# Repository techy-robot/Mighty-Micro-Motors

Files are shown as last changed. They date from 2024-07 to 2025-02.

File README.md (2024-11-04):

# Mighty Micro Motors
My goal with this project is to recreate the expensive and highly advanced motors typically found in big robots, such as in Boston Dynamics or MIT's robots, but at a **much** smaller scale. These are essentially tiny drone motors with a high reduction gearbox, a magnetic encoder, and a FOC controller board.

You can check out my project log [here](Progress%20Log.md).

This project is sponsored by [PCBWay](https://www.pcbway.com/)

## Gearbox
This has to be a resin printed or precision machined gearbox, just from the sheer smallness of everything. The brushless drone motors (HappyModel SE0802) are 10mm in diameter, so the gearbox ideally should be a similar size.

I'm currently thinking about having a cycloidal or split-ring planetary gearbox, due to the compact size and high reduction ratios

Preliminary CAD designs are on onshape, you can watch my progress here: [Mighty Micro Motors - Onshape](https://cad.onshape.com/documents/c861ec30af8169cf9c14bd7f/w/e538486c85e6a5fe77cd1d33/e/19bd07544dbaacbeb2fafd06). Step files and STL files will also be uploaded to this repo.

### Cycloidal 16-to-1 reduction:

Currently the design is twice as big as my ideal, with a 19mm diameter. I can not reduce the diameter without removing the bearings, possible reducing the lifespan. This *really* needs to be smaller, so I may do some testing and just remove some bearings. I'm not actually sure how well the 1x3x1mm bearings roll compared to just a smooth shaft. I could also cut the hole count down if the screws were also the shafts.

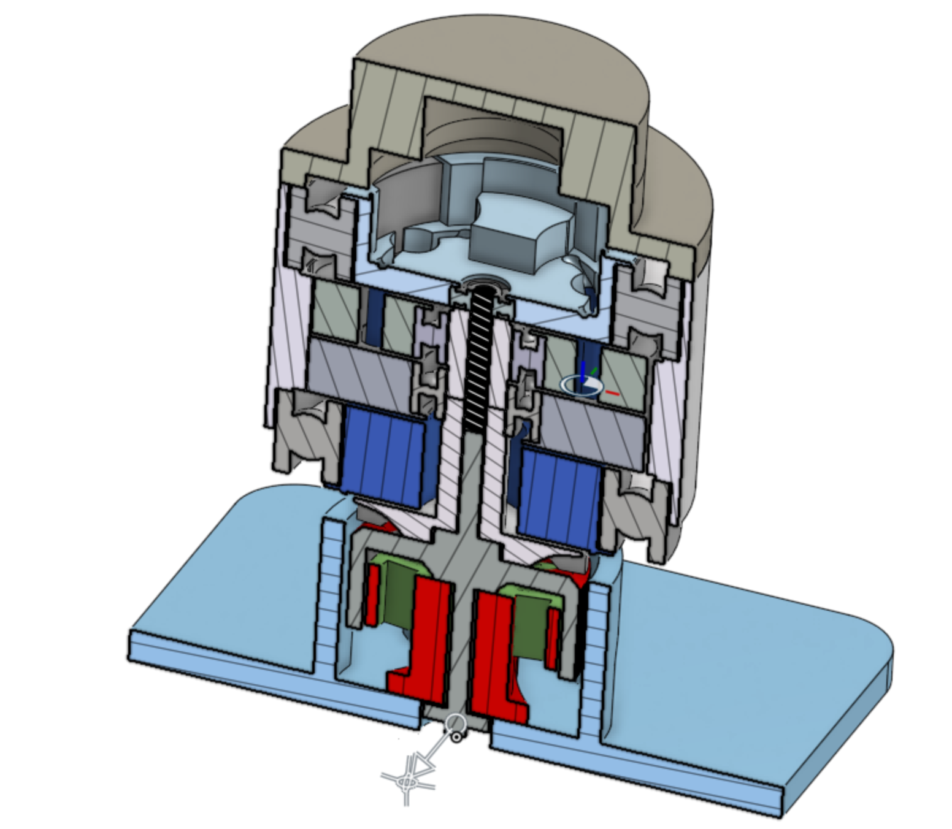
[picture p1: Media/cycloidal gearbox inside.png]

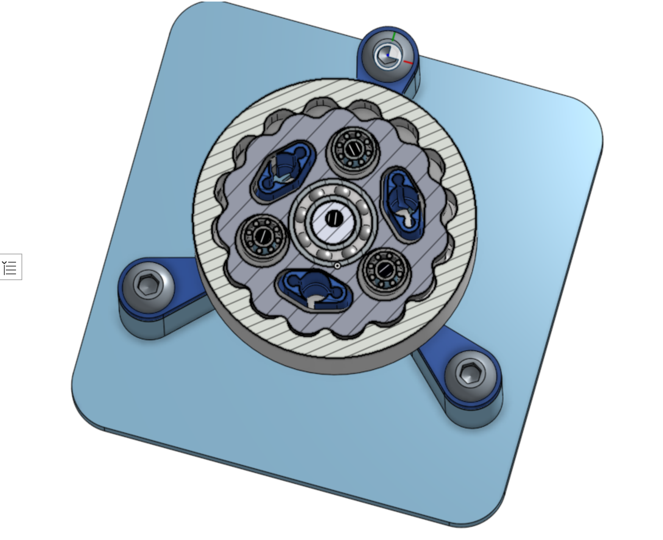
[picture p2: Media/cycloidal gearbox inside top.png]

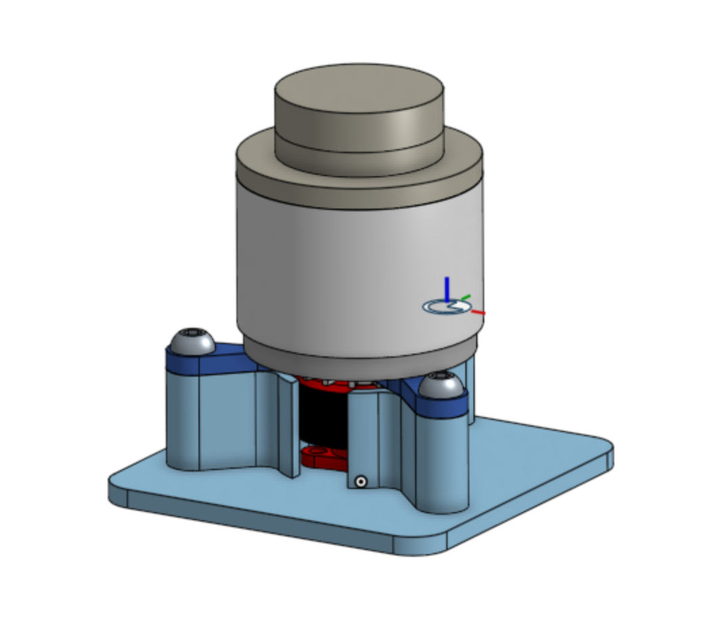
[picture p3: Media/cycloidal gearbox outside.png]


In real life:
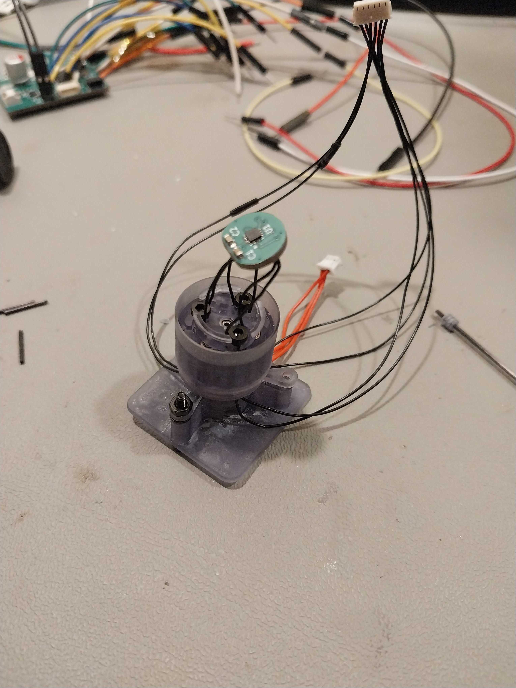
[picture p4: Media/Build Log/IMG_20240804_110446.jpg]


### Split Ring Compound Planetary gearbox 74.66-to-1 reduction:

This goes by a variety of names, but basically this is a two-stage planetary gearbox, with the planets merged together. Due to some interesting mechanics, this type of gearbox can have **an extreme** reduction ratio in a relatively small size. The reduction ratio is the first stage ratio(ring teeth / sun teeth) multiplied by 2nd stage ring teeth, divided by the number of planets (simplified, this only works if both planet gear sets have the same number of teeth). The 2nd stage is advanced by a few teeth every revolution of the first. This operates on the same principle as a cycloidal drive and a harmonic drive, but with the added reduction ratio of the planetary gears, and without the vibration.

One thing to note with this type of gearbox is that the output encoder wires cannot fit through the center like my other gearbox, which limits the usable motion range to 270 degrees.

My particular version is a 74.66:1, in a much smaller form-factor than my cycloidal drive!
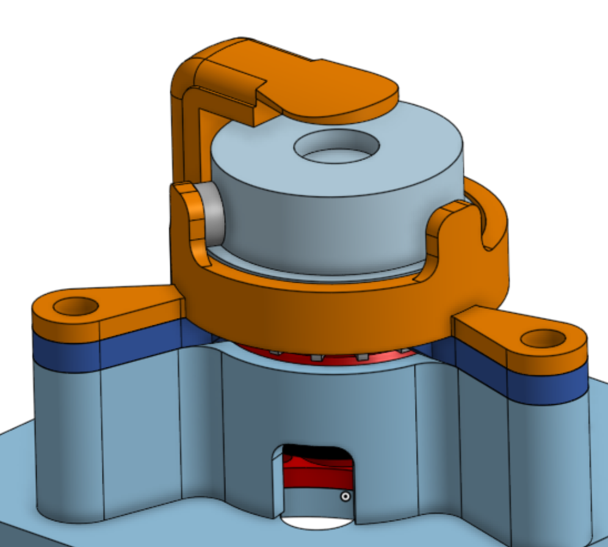
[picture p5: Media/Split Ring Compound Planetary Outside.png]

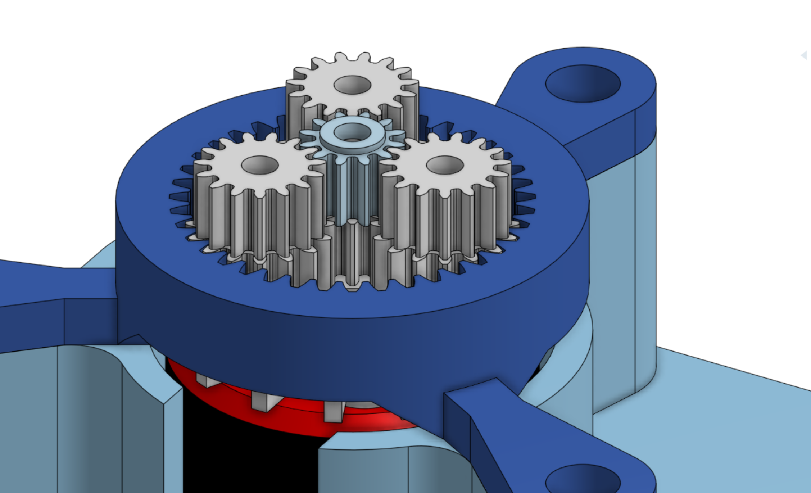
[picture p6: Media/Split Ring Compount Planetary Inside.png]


## Control board
### Version 1
My first version of the control board is designed to test all functions that may exist on a robot. I have the motor driver, a MCU for the algorithms, connectors for sensors (I2c and SPI), and a power management system.

A lot of care has been taken to design for EMI, which is why I have separate ground planes and have plotted current return paths for *most* traces. When I design a controller that supports 3+ motors I'm going to deal with length matching too on the low speed signals (Currently I'm testing all possible pin combinations, which doesn't lend itself to length matching). I'm still learning about good EMI design practices though, so there may be a big flaw in the design I don't see.

At it's current state the control PCB has been assembled and power tested. Nothing blew up or heated up, though I have discovered that the battery protection chip is not working. I will probably just bypass that circuit and move on.

[Schematic](Media/stm32g070%20and%20DRV8311%20single%20motor%20board%20-%20V1%20Alpha.pdf)

**Specs:**
- TI BQ25060 single-cell battery charger along with a BQ298012 battery protection chip. 
- 4 mosfets on board to control system power, 60+ amps of current
- TI DRV8311 motor driver, which can drive a brushless motor at 5 amps current (I fully expect heat problems due to the small size of the chip!)
- STM32G070CB, clocked at the max 64mhz (16mhz crystal scaled internally). 128kb mem, 64kb ram. The stm32 I chose is relatively inexpensive and *should be able to handle 3 motors*. (this was proven false later after testing other MCUs)

The motor driver section is 16x11mm, which hopefully is small enough and easily tileable for a small robot controller with lots of motors. The biggest part of the board is the power management, followed by the stm32.

**Ordering info**
The pcb is a 4 layer board, with 1 oz copper. Also, it is **strongly recommended** to order a stencil for both PCBs and to do a good job pasting the board. I fortunately ordered a stencil for the controller, but I put too much solder paste on and had to fix a lot of bridges after the fact. For the encoder board I manually pasted it, and that was a real pain to do a tiny QFN chip.

#### Tested functionality:
- Can be powered on without exploding
- 3.3v regulator on the motor chip works (though with a flaw that requires a kickstart to get it going)
- Can be programmed and flash an LED
- Can be clocked to a max 64mhz
- Power mosfet switching works on the charger
- Can communicate over SPI, UART and the debug interface
- Can drive a brushless drone motor at 10k rpm

#### Photos
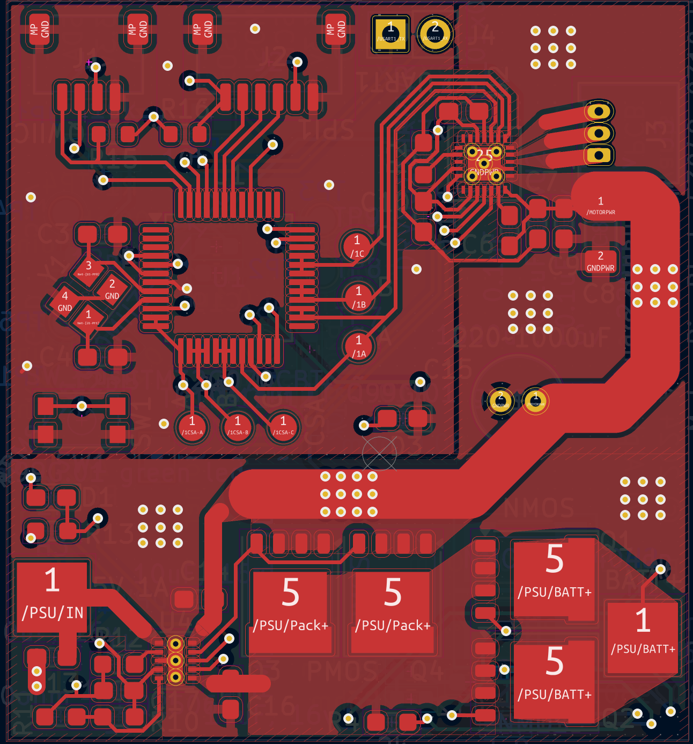
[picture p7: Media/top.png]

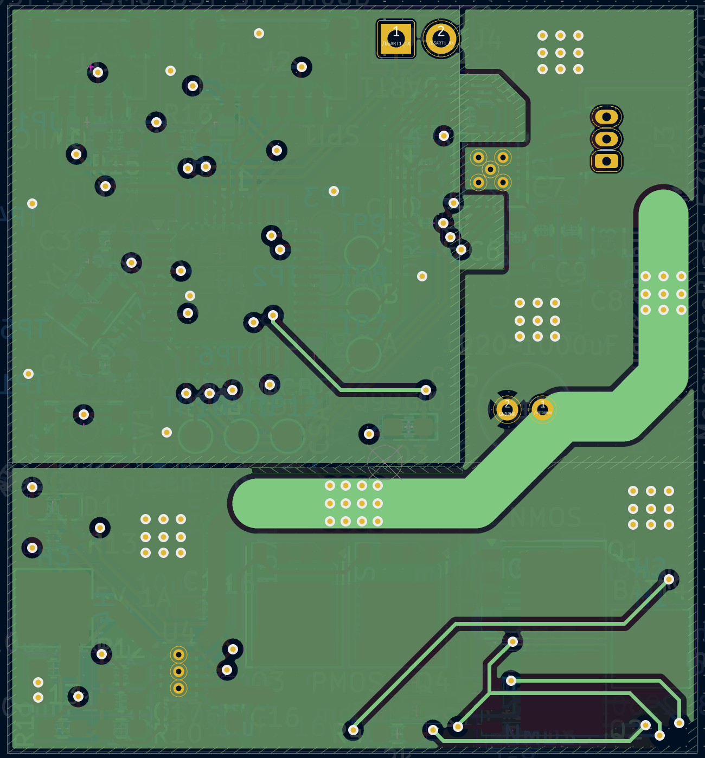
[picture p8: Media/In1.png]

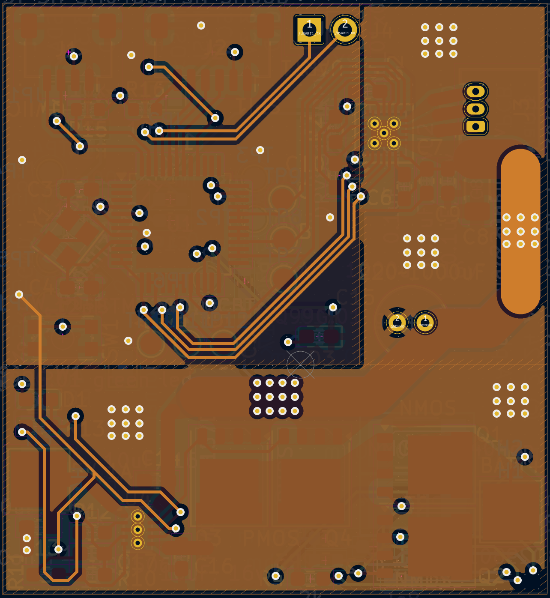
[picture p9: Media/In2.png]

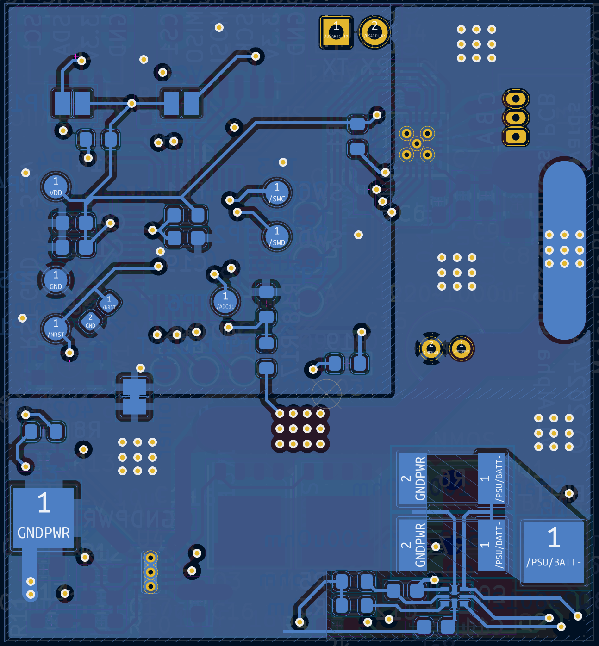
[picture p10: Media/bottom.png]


Assembled:
finished pcb

(Note that I messed up on the mosfets I ordered which were too tiny. I have the correct mosfet specified now)

### Version 2
My second test control board has had a lot of the components switched, and actually split the DRV8311 onto a separate board.

I am testing a lot of the same functionality as last time, and its still a single motor system.

[Schematic](Kicad/esp32-s3%20single%20motor%20&%20battery%20controller/esp32-s3%20single%20motor%20&%20battery%20controller.pdf)

**Specs:**
- TI BQ24780S 2-cell battery charger along with a BQ276905 battery balancer, monitor, and protection chip. 
- 2 power mosfets on board to control system power, 60+ amps of current, 4 additional smaller mosfets for charging
- ESP32-S3 microcontroller, clocked at 240mhz and can support 4 motors (not in this version)
- TI DRV8311 controlling the motor, except on a separate PCB located on the back of the motor.
- 7 pin FPC connector for the V2 encoder

#### Photos
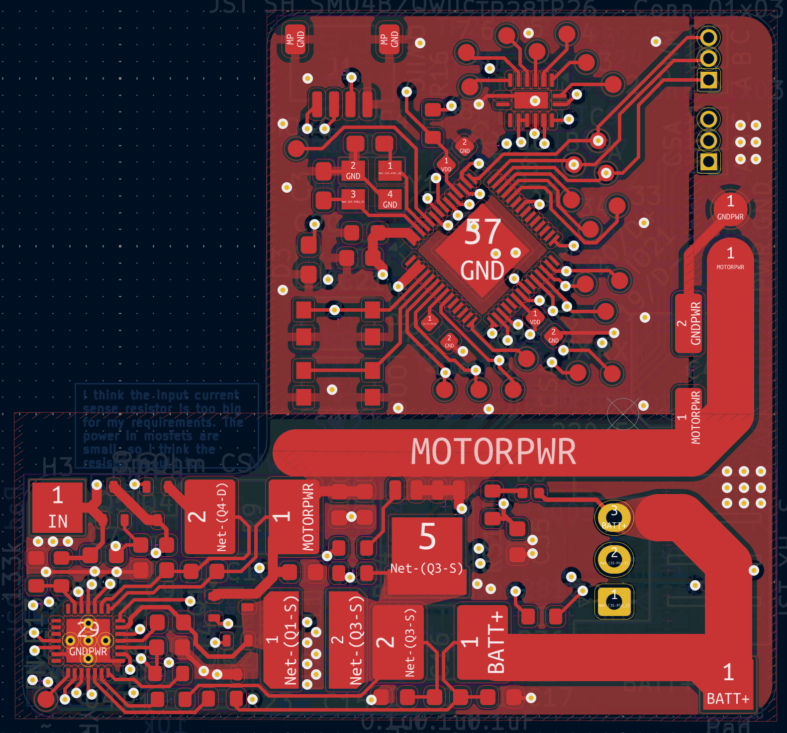
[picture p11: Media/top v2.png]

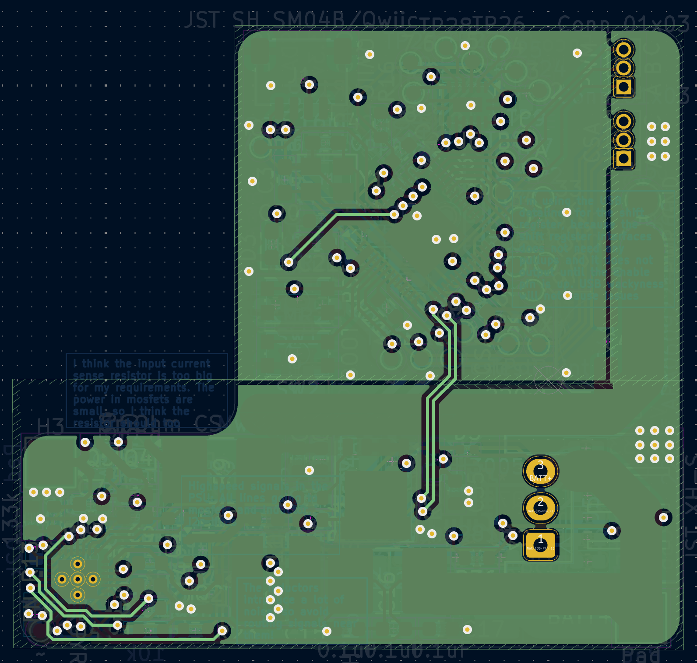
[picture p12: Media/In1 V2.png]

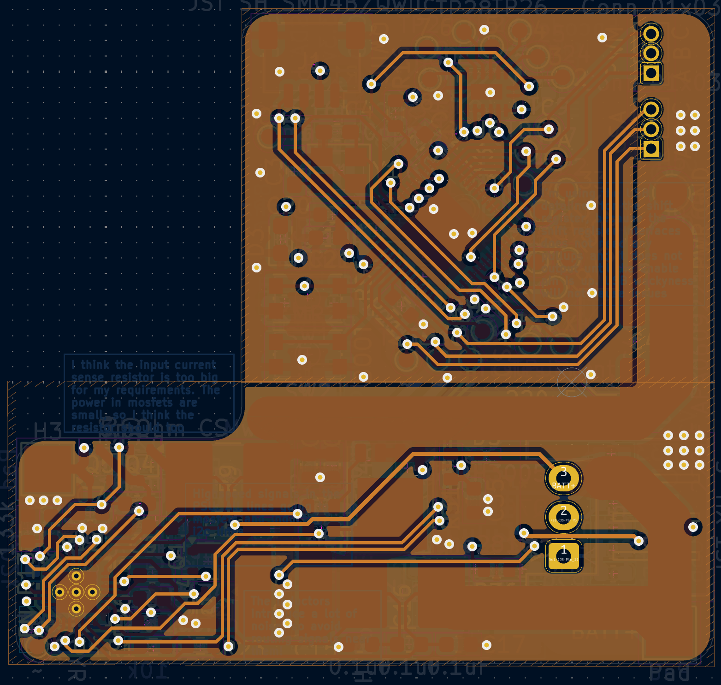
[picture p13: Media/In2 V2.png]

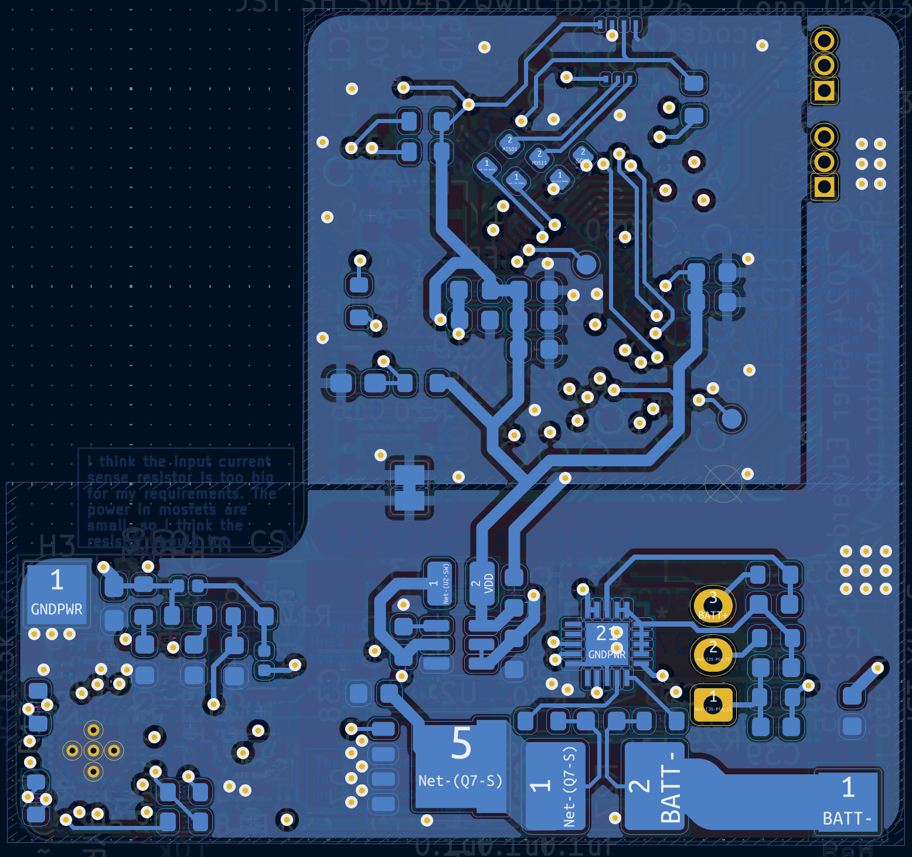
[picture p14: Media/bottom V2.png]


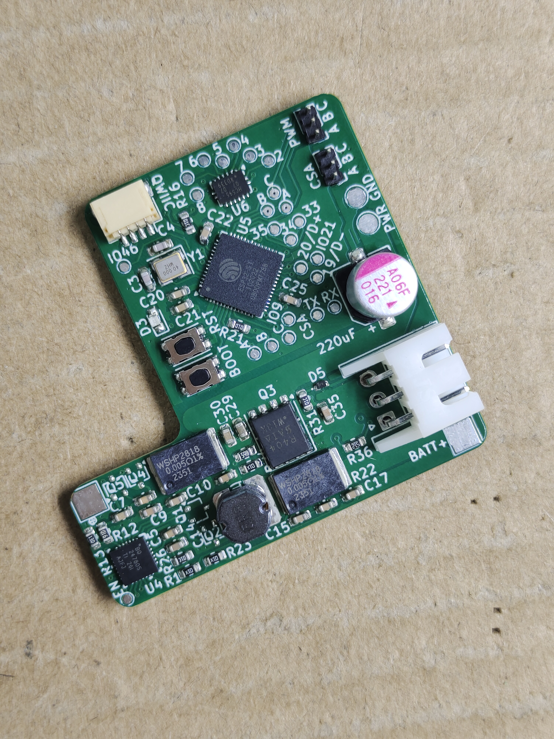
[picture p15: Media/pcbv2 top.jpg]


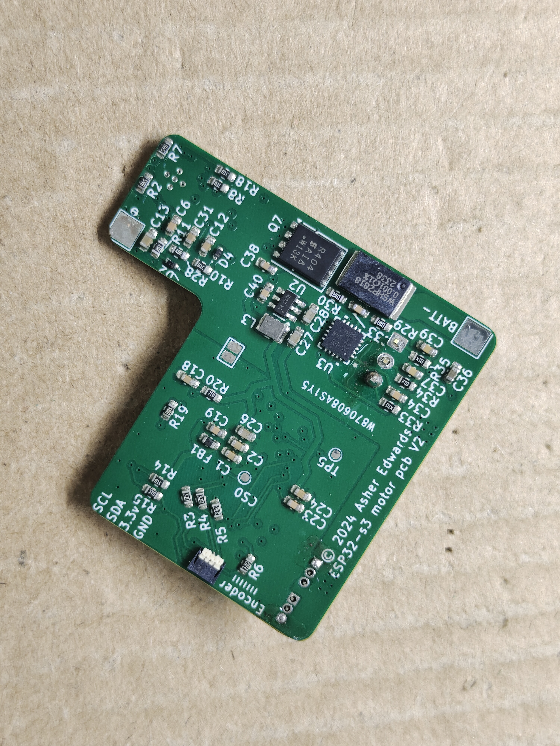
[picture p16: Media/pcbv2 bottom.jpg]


Off board controller

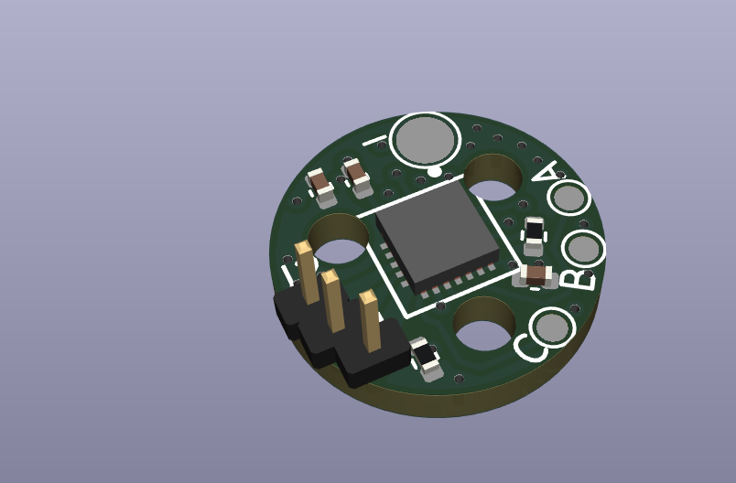
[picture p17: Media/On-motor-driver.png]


## Encoder board


This is a little magnetic board I designed to be attached to the end of the motor. It has a MA735 chip, which is low cost and seemed perfect for my needs. The resolution is inversely proportional to rotational reading speeds, so I will be fine no matter which end of the gearbox I stick it on. Low resolution on the high-speed end will mean I still have high resolution positioning on the output, and high resolution on the output side is fine because the output is slower.

The board is barely bigger than the jst sh connector on top for SPI communication! V2 of the board is mounted on a flex cable so it doesn't need wires.

The encoder chips datasheet recommends a diametrically magnetized 5x3mm neodymium magnet to operate. I used a 6x3mm from K&J magnetics: [D42DIA](https://www.kjmagnetics.com/proddetail.asp?prod=D42DIA).

## Sponsorship
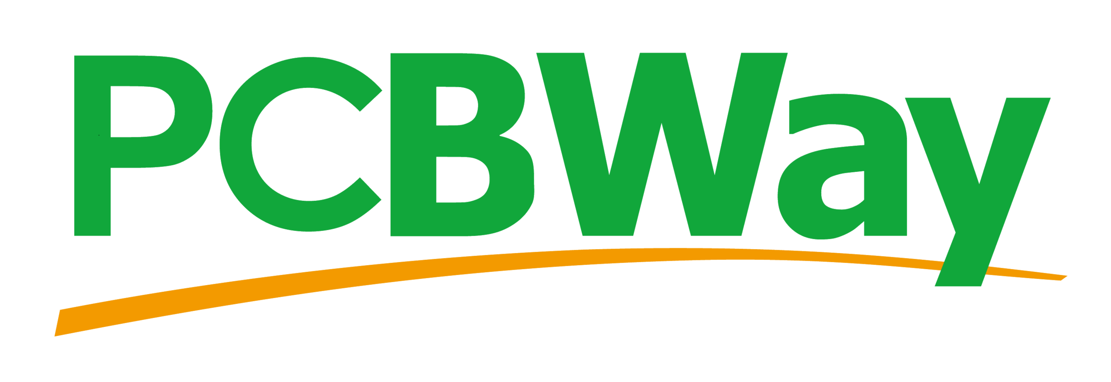
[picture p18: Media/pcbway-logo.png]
PCBWay-Logo


Thanks to PCBWay for reaching out to sponsor my project. They kindly offered to allow me to test their pcb manufacturing capabilites with this project.

I liked the quality of the pcbs I received for the V2 boards, everything was soldered correctly with only minor burn marks on the through-hole components. The assembly service they offered was also top-notch, much easier than hand assembling at home. When I made a mistake on one of the PCB assemblies I ordered, they were quick to ask what should be done, and were willing to let me have the misplaced parts (sot-23 transitors instead of sot23-5) so I could fix it myself with some bodge wires. The one downside to PCBway is the cost of the boards, I would not normally pay for prototype pcbs at their prices.

Try them out if you haven't [https://www.pcbway.com/](https://www.pcbway.com/).

See the section **Version 2/Photos** above for pictures.

## Code
There is not that much code currently, just some tests to verify the board and motors work, and a programmer definition for my Flipper Zero. I am planning on using the wonderful [SimpleFOC](https://github.com/simplefoc/Arduino-FOC) library as a starting point for the motor control, building out my own communication protocol or going with ROS 2 style communication. I may also add some motor control algorithms as I discover more.

I have tuned the PID algorithms for my particular HappyModel SE0802 brushless drone motors.

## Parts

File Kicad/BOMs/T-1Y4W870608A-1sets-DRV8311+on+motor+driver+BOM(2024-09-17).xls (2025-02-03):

PCBWay Bom Quotation, Product No.:T-1Y4W870608A
Item # | *Designator | *Qty | *Mfg Part # | *Package/Footprint | *Unit Price(1 set) | *Total | *Actual Purchase Mfg Part # | Customer Reply
1 | C1 | 1 | 4.7uF | C_0402_1005Metric | $0.381 | $0.381 | CL05A475MQ5NRNC | These need to be 16volt rated
2 | C3,C2,C6 | 3 | 0.1uF, 16v | C_0402_1005Metric | $0.025 | $0.075 | CC0402KRX5R7BB104
3 | U1 | 1 | DRV8311HRRWR | DRV8311_0.3mmVias | $1.995 | $1.995
4 | R3 | 1 | 47k | R_0402_1005Metric | $0.036 | $0.036 | RC0402FR-0747KL
5 | R2 | 1 | 100k | R_0402_1005Metric | $0.068 | $0.068 | RC0402FR-07100KL
6 | R1 | 1 | 300k | R_0402_1005Metric | $0.036 | $0.036 | RC0402FR-07300KL
7 | C7 | 1 | 0.1uF | C_0402_1005Metric | $0.076 | $0.076 | CC0402KRX5R7BB104
8 | C5,C4 | 2 | 22uF | C_0402_1005Metric | $1.310 | $2.620 | GRM155R60J226ME11D | I need to swap these out for 4.7uF, 16volt rated capacitors
 |  |  |  |  | Component Cost | $5.29

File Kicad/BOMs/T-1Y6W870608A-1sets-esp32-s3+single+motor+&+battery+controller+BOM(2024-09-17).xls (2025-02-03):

PCBWay Bom Quotation, Product No.:T-1Y6W870608A
Item # | *Designator | *Qty | *Mfg Part # | *Package/Footprint | *Unit Price(1 set) | *Total | *Delivery Time | *Actual Purchase Mfg Part # | *PCBWay Note | Customer Reply
1 | C3,C4 | 2 | 16pF | C_0603_1608Metric_Pad1.08x0.95mm_HandSolder | $0.162 | $0.324 |  | TCC0603COG160J500CT
2 | Y1 | 1 | 40mhz, 10ppm | Crystal_SMD_3225-4Pin_3.2x2.5mm | $0.801 | $0.801 |  | TX322540M4FBCE2T | we will supply is TX322540M4FBCE2T ,OK? please confirm | Good
3 | C9,C15,C16,C10,C25,C20,C11,C22,C17,C33,C23,C38,C19 | 13 | 0.1uF | C_0603_1608Metric | $0.007 | $0.091 |  | CC0603KRX7R6BB104
4 | J4,J3 | 2 | Conn_01x03 | PinHeader_1x03_P1.27mm_Vertical | $0.125 | $0.250 |  | B-2101S03P-A110 | we will supply is B-2101S03P-A110 ,OK? please confirm | Good
5 | R24,R1,R23,R35,R33,R34 | 6 | 10ohm | R_0603_1608Metric | $0.071 | $0.426 |  | RC0603FR-0710RL
6 | C21,C2,C1,C24 | 4 | 1uF | C_0603_1608Metric | $0.040 | $0.160 |  | TCC0603X5R105K100CT
7 | R26,R16,R31,R10,R14,R20,R8,R18,R15 | 9 | 10k | R_0603_1608Metric | $0.014 | $0.126 |  | RC0603FR-0710KL
8 | J1 | 1 | JST SH SM04B/Qwiic | JST_SH_SM04B-SRSS-TB_1x04-1MP_P1.00mm_Horizontal | $0.769 | $0.769 |  | SM04B-SRSS-TB
9 | TP3,TP2,TP18,TP4,TP22 | 5 | ~ | TestPoint_Pad_D1.0mm |  |  |  |  | [DNP不要贴];
10 | R21 | 1 | 100k | R_0603_1608Metric | $0.123 | $0.123 |  | RC0603FR-07100KL
11 | R9 | 1 | 5mOhm CS wshp2818 | R_2816_7142Metric |  |  |  |  | Please provide exact part number or component URL. | Vishay WSHP28185L000FEA
12 | D3 | 1 | Osram LT Q99G.01 green led | LED_0603_1608Metric_Pad1.05x0.95mm_HandSolder | $0.714 | $0.714 | 7-10 Workdays | LT Q99G.01-R2T1-25-1-5-R18 | Part we will supply is LT Q99G.01-R2T1-25-1-5-R18， pls confirm. | Good
13 | Q1,Q5,Q4,Q2 | 4 | PJA3430 | SOT-323_SC-70 |  |  |  |  | we haven't found this part number, could you please double check? | PJA3430_R1_00001, from Panjit International
14 | R25 | 1 | 4.02kohm | R_0603_1608Metric | $0.154 | $0.154 |  | RC0603FR-074K02L
15 | U4 | 1 | BQ24780SRUYR | RUY0028A | $0.714 | $0.714
16 | C5 | 1 | 47nF | C_0603_1608Metric | $0.109 | $0.109 |  | CC0603KRX7R8BB473
17 | SW2,SW1 | 2 | KMR2 | SW_Push_1P1T_NO_CK_KMR2 |  |  |  |  | It has multiple suffixes, please provide the complete model number | KMR231NG ULC LFS
18 | L2 | 1 | 5.6uH Bourns SDE0604A | L_Bourns_SDR0604 | $0.483 | $0.483 | 7-10 Workdays | SDE0604A-5R6M | Part we will supply is SDE0604A-5R6M, pls confirm. | Good
19 | J5 | 1 | JST XH-S | JST_XH_S3B-XH-A_1x03_P2.50mm_Horizontal | $0.200 | $0.200 | 7-10 Workdays | S3B-XH-A
20 | C8 | 1 | 47nf | C_0603_1608Metric | $0.109 | $0.109 |  | CC0603KRX7R8BB473
21 | C41 | 1 | 220uF,APA0609221M016R | CP_Elec_6.3x9.9 | $4.370 | $4.370 | 7-10 Workdays | APA0609221M016R
22 | U5 | 1 | ESP32-S3 | QFN-56-1EP_7x7mm_P0.4mm_EP4x4mm | $2.170 | $2.170
23 | C14,C35,C6,C31 | 4 | 2.2uf | C_0603_1608Metric | $0.081 | $0.324 |  | CC0603KRX5R6BB225
24 | Q3,Q7 | 2 | Vishay sir404dp | PQFN-8-EP_6x5mm_P1.27mm_Generic | $2.092 | $4.184 | 7-10 Workdays | SIR404DP-T1-GE3 | Part we will supply is SIR404DP-T1-GE3 , pls confirm. | Good
25 | R12 | 1 | 866k | R_0603_1608Metric | $0.207 | $0.207 |  | RC0603FR-07866KL
26 | C29,C30,C36 | 3 | 10uF | C_0603_1608Metric | $0.071 | $0.213 |  | 0603X106M100NT
27 | D5,D2,D4 | 3 | GSDH3005 | D_0402_1005Metric | $0.491 | $1.473 | 7-10 Workdays
28 | R13 | 1 | 133k | R_0603_1608Metric | $0.097 | $0.097 |  | RC0603FR-07133KL
29 | U6 | 1 | 74HC595 | DHVQFN-16-1EP_2.5x3.5mm_P0.5mm_EP1x2mm | $0.297 | $0.297
30 | C7 | 1 | 1nF | C_0603_1608Metric | $0.075 | $0.075 |  | CC0603KRX7R7BB102
31 | R22 | 1 | 5mOhm, CS wshp2818 | R_2816_7142Metric |  |  |  |  | Please provide exact part number or component URL. | Vishay WSHP28185L000FEA
32 | R36 | 1 | 5.1k | R_0603_1608Metric | $0.049 | $0.049 |  | RC0603FR-075K1L
33 | R11,R28 | 2 | 2ohm | R_0603_1608Metric | $0.061 | $0.122 |  | RC0603FR-072RL
34 | L1 | 1 | GND joiner | SolderJumper-2_P1.3mm_Bridged_Pad1.0x1.5mm |  |  |  |  | [DNP不要贴];
35 | R4,R5,R3,R6 | 4 | 33ohm | R_0603_1608Metric | $0.017 | $0.068 |  | AC0603FR-0733RL
36 | C28,C27 | 2 | 22uf | C_0603_1608Metric | $0.289 | $0.578 |  | CL10A226MQ8NRNE
37 | C40 | 1 | 100nF | C_0603_1608Metric | $0.085 | $0.085 |  | CC0603KRX7R6BB104
38 | C34 | 1 | 22nF | C_0603_1608Metric | $0.090 | $0.090 |  | CC0603KRX7R9BB223
39 | C13 | 1 | 10uF, 16v | C_0603_1608Metric_Pad1.08x0.95mm_HandSolder | $0.878 | $0.878 |  | CL10A106MO8NQNC
40 | L3 | 1 | 4.7uH, MAMK2520T4R7M | L_1008_2520Metric | $0.338 | $0.338 | 7-10 Workdays | MAMK2520T4R7M
41 | C39,C37 | 2 | 220nF | C_0603_1608Metric | $0.097 | $0.194 |  | CC0603KRX7R6BB224
42 | C26 | 1 | 22uF | C_0603_1608Metric | $0.578 | $0.578 |  | CL10A226MQ8NRNE
43 | C12 | 1 | 1uf | C_0603_1608Metric | $0.161 | $0.161 |  | TCC0603X5R105K100CT
44 | C18 | 1 | 1uF | C_0603_1608Metric_Pad1.08x0.95mm_HandSolder | $0.161 | $0.161 |  | TCC0603X5R105K100CT
45 | R29,R30 | 2 | 100ohm | R_0603_1608Metric | $0.017 | $0.034 |  | RC0603FR-07100RL
46 | R27 | 1 | 1mOhm, CS wshp2818 | R_2816_7142Metric |  |  |  |  | Please provide exact part number or component URL. | Vishay WSHP28181L000FEA
47 | R2,R7 | 2 | 4.02k | R_0603_1608Metric | $0.077 | $0.154 |  | RC0603FR-074K02L
48 | J2 | 1 | 7 pin FPC 0.3mm Panasonic Y3b | fpc_7pin_0.3mm_connector Panasonic |  |  |  |  | Please provide exact part number or component URL. | AYF330735
49 | FB1 | 1 | 120ohm imp @100mhz | L_0603_1608Metric | $0.058 | $0.058 |  | BLM18PG121SN1D | we will supply is BLM18PG121SN1D,OK? please confirm | Good
50 | U3 | 1 | BQ76905RGRR | VQFN20_RGR_TEX | $2.221 | $2.221 | 7-10 Workdays
51 | U2 | 1 | AP63203WU | TSOT-23-6 | $0.505 | $0.505 |  | AP63203WU-7 | we will supply is AP63203WU-7,OK? please confirm | Good
52 | R19 | 1 | 80.6 ohm | R_0603_1608Metric | $0.098 | $0.098 |  | RC0603FR-0780R6L
 |  |  |  |  | Component Cost | $25.33

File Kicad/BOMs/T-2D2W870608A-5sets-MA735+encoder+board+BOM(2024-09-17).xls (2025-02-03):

PCBWay Bom Quotation, Product No.:T-2D2W870608A
Item # | *Designator | *Qty | *Mfg Part # | *Package/Footprint | *Unit Price(5 sets) | *Total | *Delivery Time | *Actual Purchase Mfg Part # | Customer Reply
1 | U1 | 1 | MA735GGU-Z | UTQFN-14_MA735_MNP | $4.398 | $21.990 | 7-10 Workdays
2 | C2 | 1 | 0.1uF | C_0402_1005Metric | $0.015 | $0.075 |  | CC0402KRX7R7BB104
3 | C1 | 1 | 1uF | C_0402_1005Metric | $0.065 | $0.325 |  | CL05A105KA5NQNC
 |  |  |  |  | Component Cost | $22.39

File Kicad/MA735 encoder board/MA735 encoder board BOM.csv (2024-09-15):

Id | Designator | Footprint | Quantity | Designation | Supplier and ref
1 | U1 | UTQFN-14_MA735_MNP | 1 | MA735GGU-Z
2 | C2 | C_0402_1005Metric | 1 | 0.1uF
3 | C1 | C_0402_1005Metric | 1 | 1uF

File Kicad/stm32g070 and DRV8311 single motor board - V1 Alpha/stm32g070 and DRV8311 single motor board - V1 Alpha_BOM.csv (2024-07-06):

Reference | Value | Datasheet | Footprint | Qty | DNP
C1,C10,C18,C19 | 0.1uF | ~ | -- mixed values -- | 4
C2,C5 | 4.7uF | ~ | -- mixed values -- | 2
C3,C4 | 12pF | ~ | Capacitor_SMD:C_0603_1608Metric_Pad1.08x0.95mm_HandSolder | 2
C6,C7,C9 | 0.1uF, 16v | ~ | Capacitor_SMD:C_0603_1608Metric_Pad1.08x0.95mm_HandSolder | 3
C11 | 8nF | ~ | Capacitor_SMD:C_0603_1608Metric | 1
C12 | 1uF, 16v | ~ | Capacitor_SMD:C_0603_1608Metric | 1
C13,C14,C16 | 10uF, 16v | ~ | Capacitor_SMD:C_0603_1608Metric_Pad1.08x0.95mm_HandSolder | 3
C15 | 1000uF, 16v | ~ | Capacitor_THT:C_Radial_D5.0mm_H5.0mm_P2.00mm | 1
C17 | 1uF | ~ | Capacitor_SMD:C_0603_1608Metric_Pad1.08x0.95mm_HandSolder | 1
D1,D3 | Osram LT Q99G.01 green led | ~ | LED_SMD:LED_0603_1608Metric_Pad1.05x0.95mm_HandSolder | 2
FB1 | 120ohm imp @100mhz | ~ | Inductor_SMD:L_0603_1608Metric | 1
J1 | JST SH SM04B | ~ | Connector_JST:JST_SH_SM04B-SRSS-TB_1x04-1MP_P1.00mm_Horizontal | 1
J2 | JST SH SM06B | ~ | Connector_JST:JST_SH_SM06B-SRSS-TB_1x06-1MP_P1.00mm_Horizontal | 1
J3 | Molex_PicoBlade_53048-0310 Horizontal 3P | ~ | Connector_Molex:Molex_PicoBlade_53048-0310_1x03_P1.25mm_Horizontal | 1
J4 | Conn_01x02_Pin | ~ | Connector_PinHeader_2.54mm:PinHeader_1x02_P2.54mm_Vertical | 1
L1 | GND joiner | ~ | Jumper:SolderJumper-2_P1.3mm_Bridged_Pad1.0x1.5mm | 1
Q1 | NMOS, sir404dp | https://ngspice.sourceforge.io/docs/ngspice-html-manual/manual.xhtml#cha_MOSFETs | Package_DFN_QFN:PQFN-8-EP_6x5mm_P1.27mm_Generic | 1
Q2 | NMOS | https://ngspice.sourceforge.io/docs/ngspice-html-manual/manual.xhtml#cha_MOSFETs | Package_DFN_QFN:PQFN-8-EP_6x5mm_P1.27mm_Generic | 1
Q3 | PMOS,Si7157DP | https://ngspice.sourceforge.io/docs/ngspice-html-manual/manual.xhtml#cha_MOSFETs | Package_DFN_QFN:PQFN-8-EP_6x5mm_P1.27mm_Generic | 1
Q4 | PMOS | https://ngspice.sourceforge.io/docs/ngspice-html-manual/manual.xhtml#cha_MOSFETs | Package_DFN_QFN:PQFN-8-EP_6x5mm_P1.27mm_Generic | 1
R1,R17 | 100k | ~ | Resistor_SMD:R_0603_1608Metric | 2
R2 | 47k | ~ | Resistor_SMD:R_0603_1608Metric_Pad0.98x0.95mm_HandSolder | 1
R3 | 20ohm | ~ | Resistor_SMD:R_0603_1608Metric | 1
R4,R13 | 2k | ~ | Resistor_SMD:R_0603_1608Metric_Pad0.98x0.95mm_HandSolder | 2
R5 | 300ohm | ~ | Resistor_SMD:R_0603_1608Metric | 1
R6 | Same, 1000uOhm | ~ | vishay_wslf:RES_WSLF2512_VIS-M | 1
R7 | Vishay WSLF2512, 1%, 300uOhm | ~ | vishay_wslf:RES_WSLF2512_VIS-M | 1
R8 | 402 ohm | ~ | Resistor_SMD:R_0603_1608Metric | 1
R9,R18 | 150k | ~ | Resistor_SMD:R_0603_1608Metric | 2
R10,R12 | 1k | ~ | Resistor_SMD:R_0603_1608Metric_Pad0.98x0.95mm_HandSolder | 2
R11 | 230ohm | ~ | Resistor_SMD:R_0603_1608Metric_Pad0.98x0.95mm_HandSolder | 1
R14,R15,R16 | 10k | ~ | Resistor_SMD:R_0603_1608Metric | 3
R19 | 80.6 ohm | ~ | Resistor_SMD:R_0603_1608Metric | 1
SW1 | SW_Push | ~ | Button_Switch_SMD:SW_Push_1P1T_NO_CK_KMR2 | 1
TP1,TP2,TP3,TP4,TP5,TP6 | TestPoint | ~ | TestPoint:TestPoint_Pad_D1.5mm | 6
TP7,TP8,TP9,TP10,TP11,TP12 | ~ | ~ | TestPoint:TestPoint_Pad_D1.5mm | 6
U1 | STM32G070CBTr | https://www.st.com/resource/en/datasheet/stm32g070cb.pdf | Package_QFP:LQFP-48_7x7mm_P0.5mm | 1
U2 | DRV8311HRRWR | https://www.ti.com/lit/ds/symlink/drv8311.pdf | custom_Driver_Motor:DRV8311_0.3mmVias | 1
U3 | BQ298012RUGT | BQ298000RUGT | bq298rugt:RUG8_TEX | 1
U4 | BQ25060 | https://www.ti.com/lit/ds/symlink/bq25060.pdf | custom_Power:WSON-10-1EP_2x3mm_P0.5mm_EP0.84x2.4mm_ThermalVias_0.3mm | 1
Y1 | ABM8-16.000MHZ-10-1-U-T | ~ | Crystal:Crystal_SMD_Abracon_ABM8G-4Pin_3.2x2.5mm | 1

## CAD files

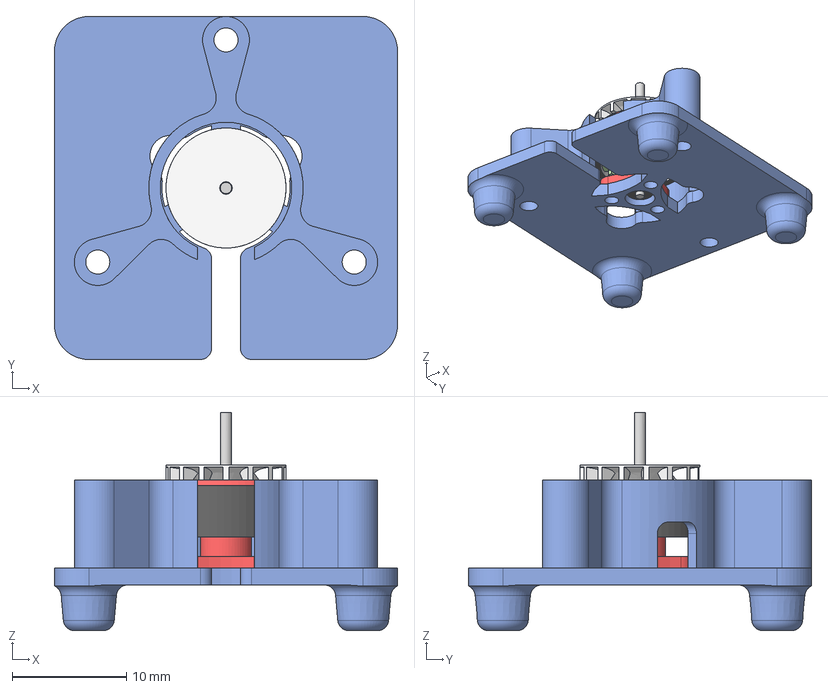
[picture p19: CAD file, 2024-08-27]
CAD/base motor assembly.step
30.0 x 30.0 x 19.1 mm
motor mount
Motor
bell
center shaft

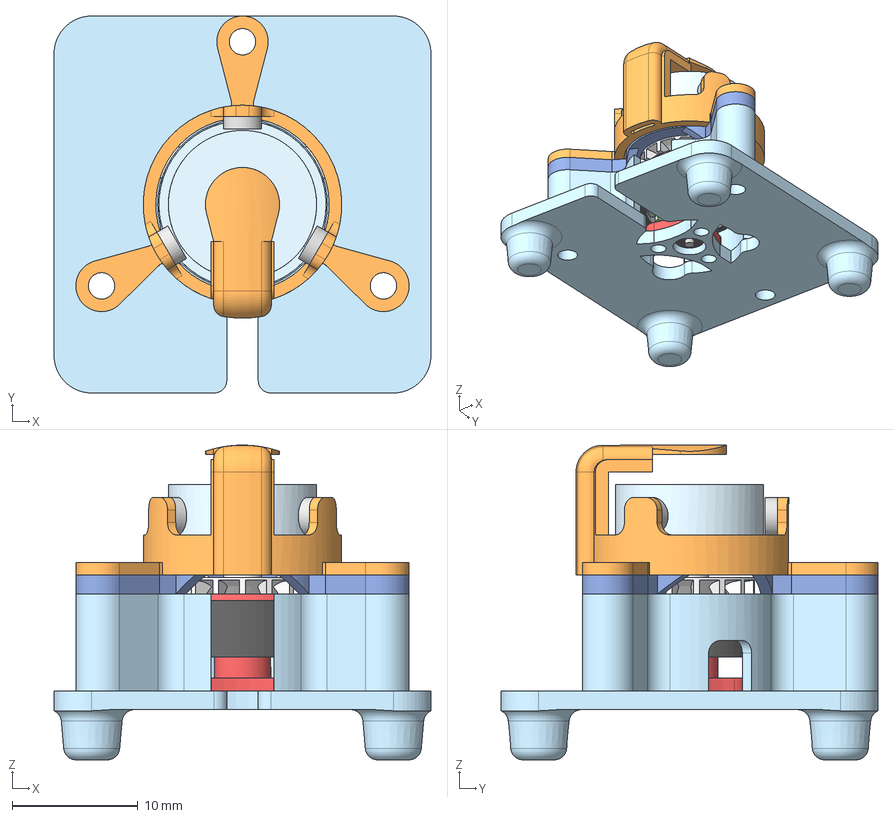
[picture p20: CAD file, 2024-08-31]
CAD/Test Gearboxes/Split Ring Compound Planetary Assembly.step
30.0 x 30.0 x 25.0 mm
compound planet x 3
Bearing x 3
2nd stage output
2nd stage sun
motor mount
output shaft holder
center shaft bottom
carrier
bell
Motor
base gearbox plate

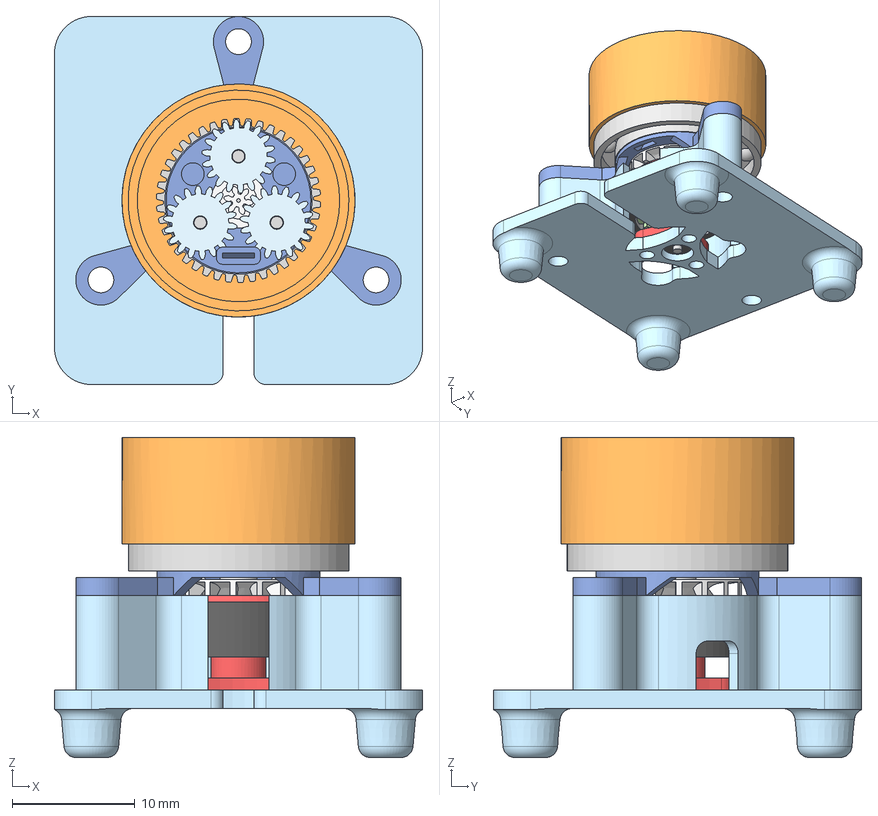
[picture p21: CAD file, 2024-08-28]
CAD/Test Gearboxes/Planetary assembly.step
30.0 x 30.0 x 26.1 mm
motor mount
rod x 3
Bearing x 4
center shaft bottom
Motor
bell
Spur gear (18 teeth) x 3
output gear
base gearbox plate

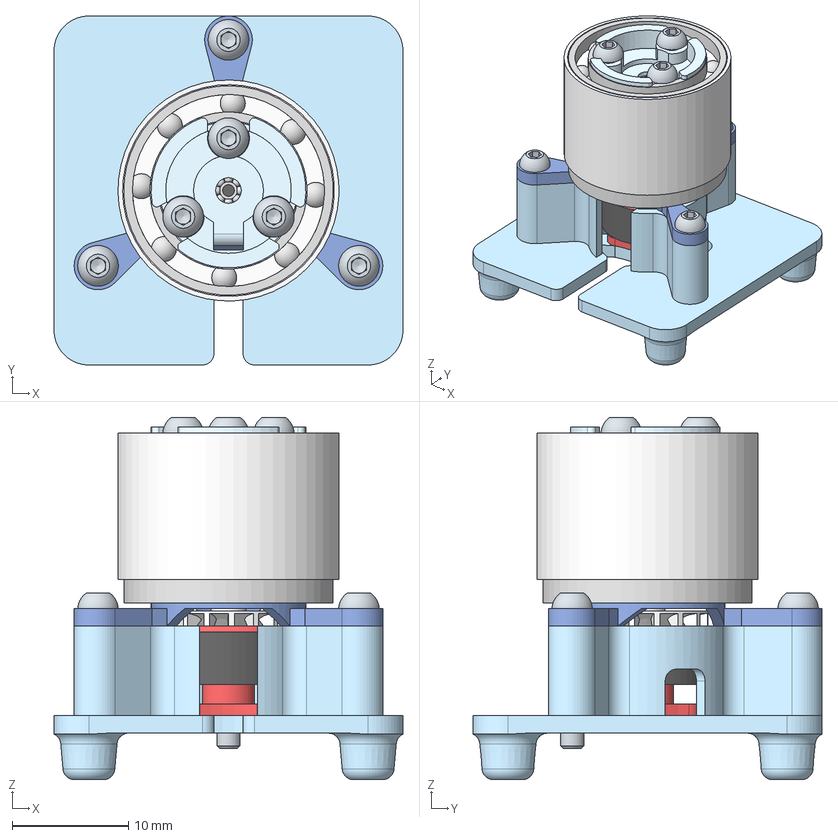
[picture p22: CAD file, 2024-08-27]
CAD/Test Gearboxes/Cycloidal Assembly.step
30.0 x 30.0 x 31.2 mm
center shaft top
Carbon fiber rod
Bearing x 5
Socket button head screw M2x0.4 x 12 x 6
center shaft bottom
1st disk
motor mount
base gearbox plate
bell
Motor
top
output disc
2nd disc

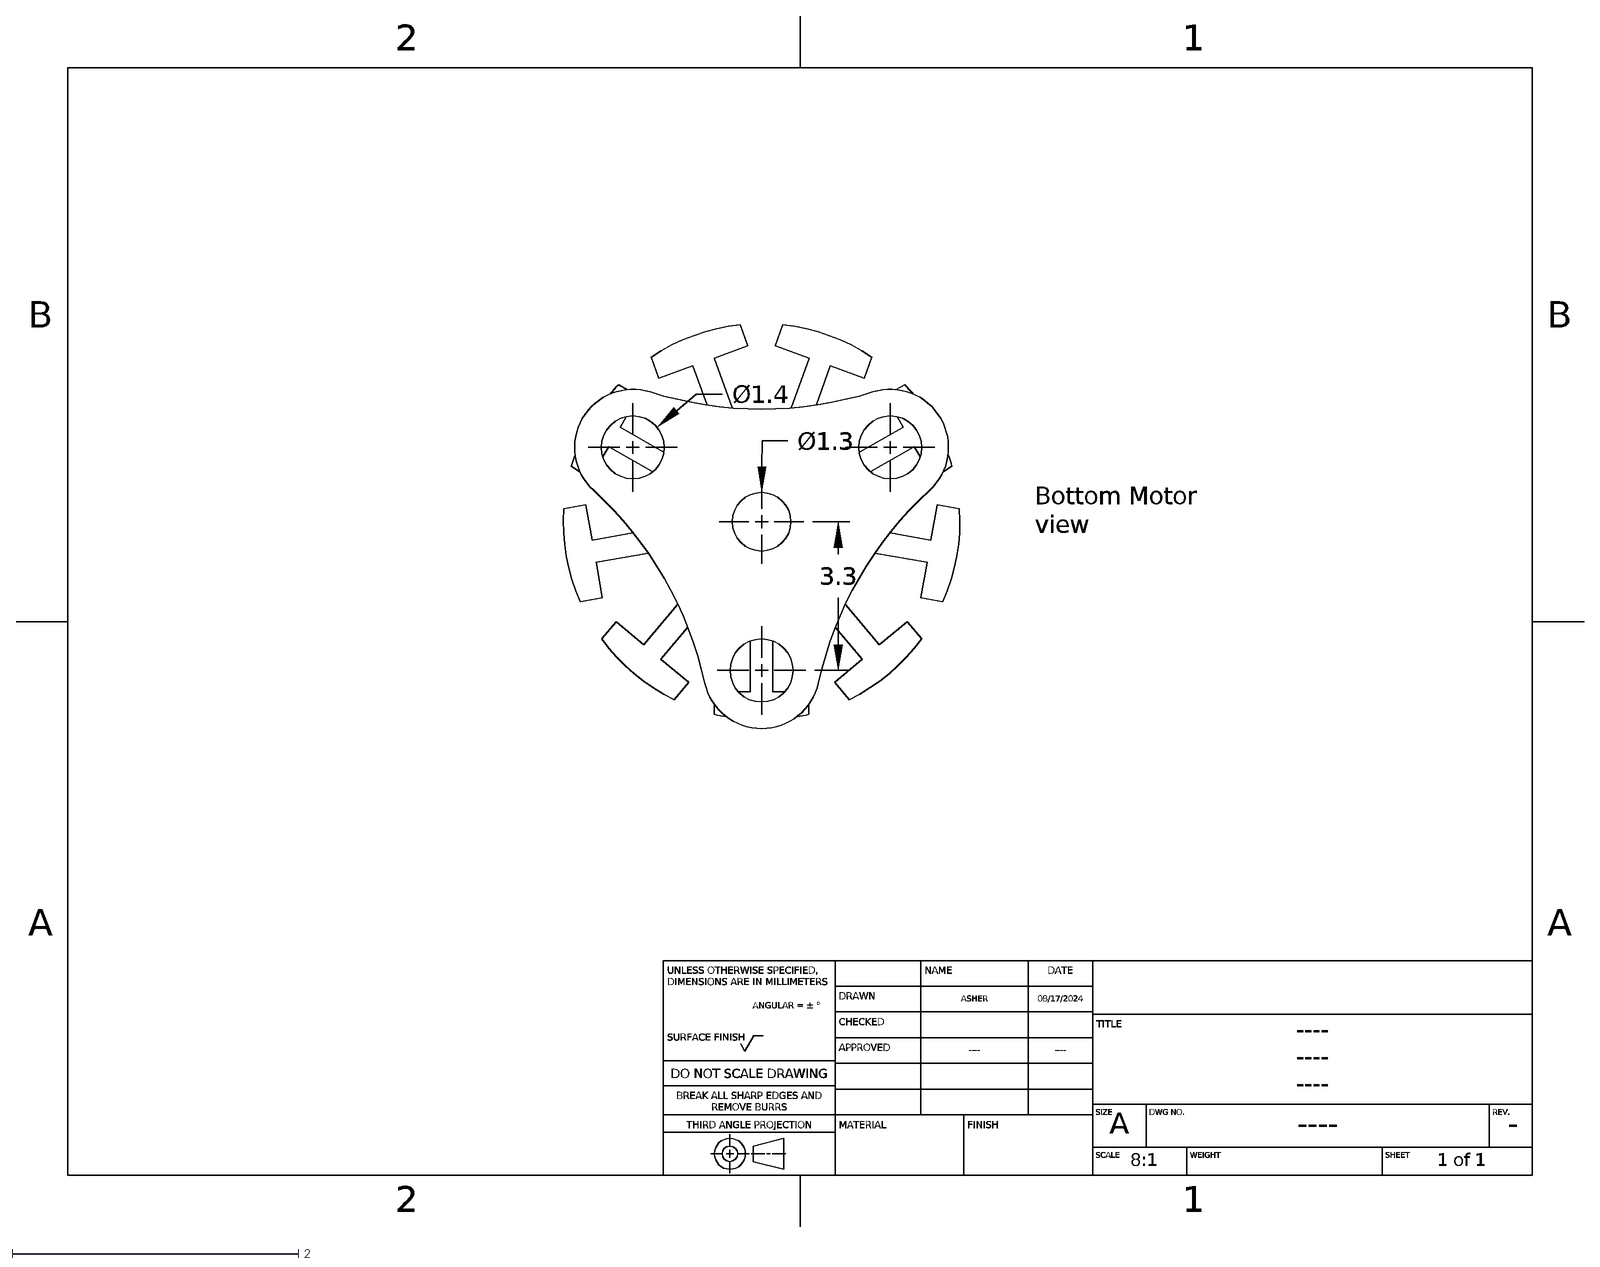
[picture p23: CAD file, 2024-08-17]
CAD/Electrical Parts/Bottom motor Drawing.dxf
2
1
A
B
UNLESS OTHERWISE SPECIFIED, DIMENSIONS ARE IN MILLIMETERS
ANGULAR = ± °
SURFACE FINISH
DO NOT SCALE DRAWING
BREAK ALL SHARP EDGES AND REMOVE BURRS
THIRD ANGLE PROJECTION
NAME
DATE
DRAWN
ASHER
08/17/2024
CHECKED
APPROVED
----
MATERIAL
FINISH
TITLE
SIZE
DWG NO.
REV.
-
SCALE
8:1
WEIGHT
SHEET
1 of 1
Bottom Motor view
3.3
Ø1.3
Ø1.4

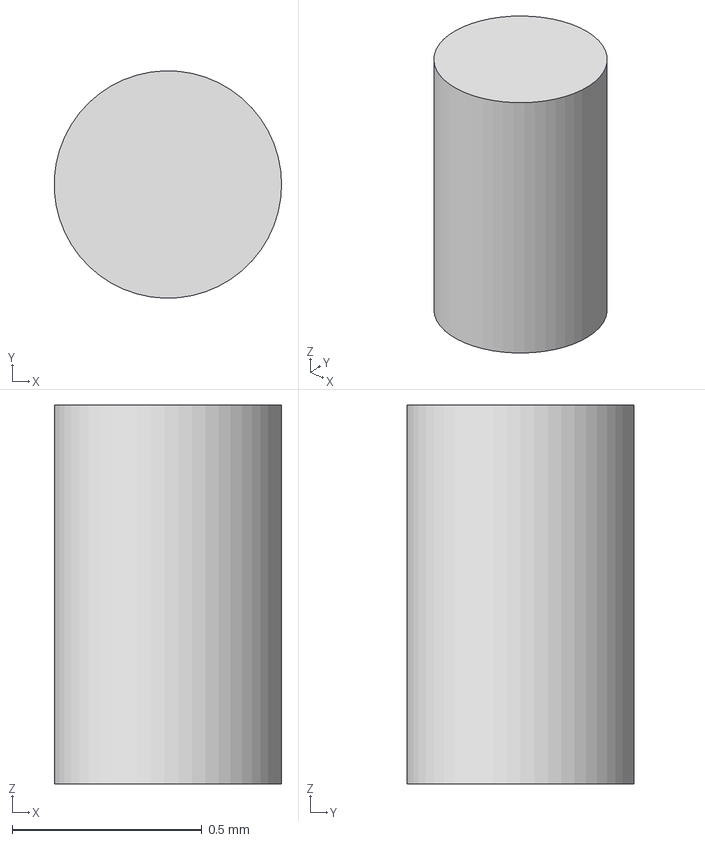
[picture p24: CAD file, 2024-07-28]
CAD/Mechanical Parts/Carbon Fiber Rod.step
0.599 x 0.6 x 1.00 mm

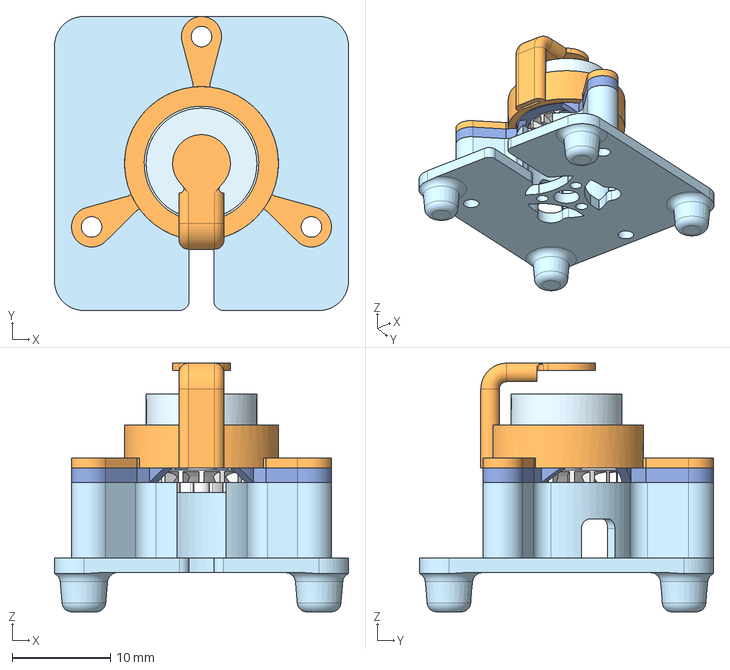
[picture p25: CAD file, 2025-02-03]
CAD/Test Gearboxes/Split Ring Compound Planetary.step
30.0 x 30.0 x 25.4 mm

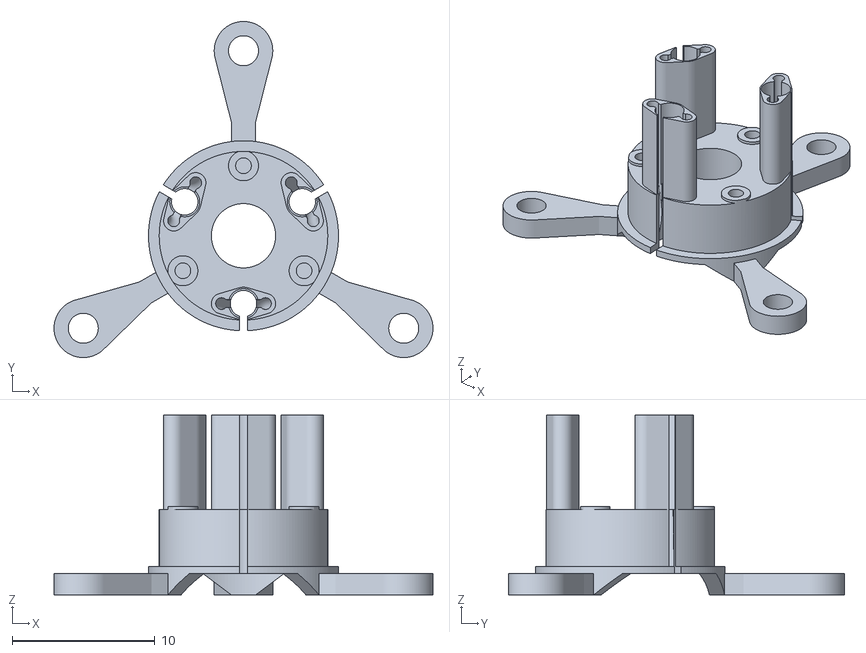
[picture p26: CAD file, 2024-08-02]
Print files/Cycloidal/Cycloidal - base gearbox plate.stl
26.5 x 23.5 x 12.6

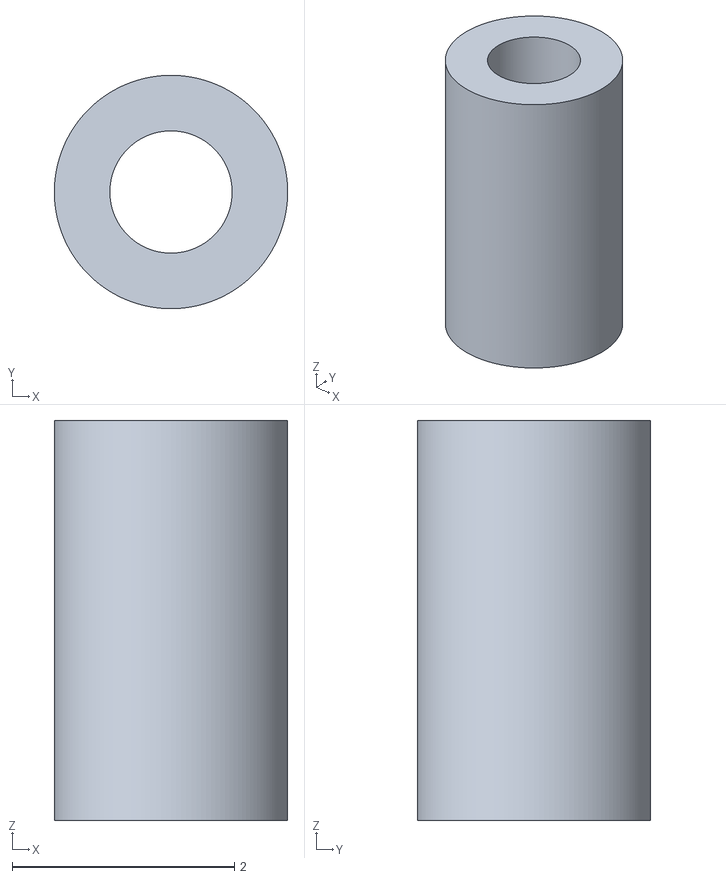
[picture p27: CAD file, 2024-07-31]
Print files/Spacer x3.stl
2.10 x 2.10 x 3.60

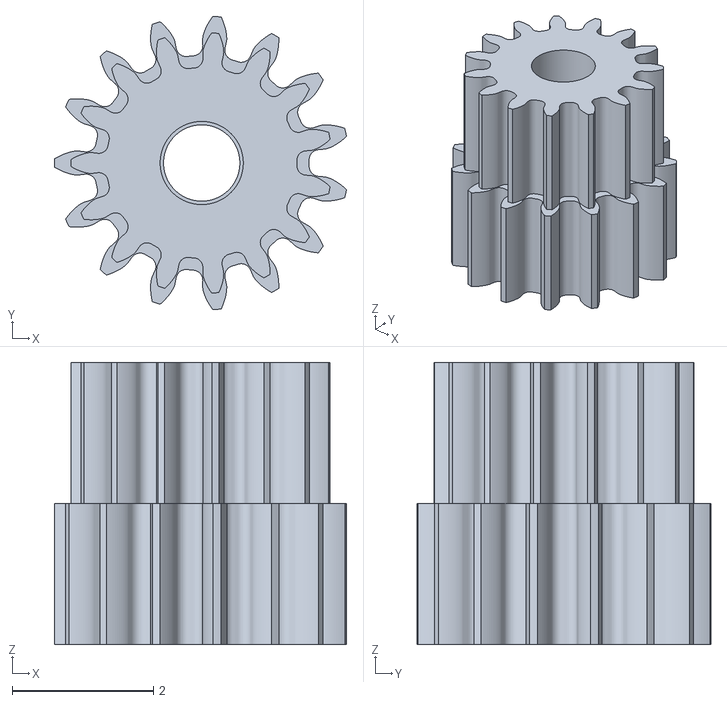
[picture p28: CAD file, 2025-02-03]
Print files/Split Ring Compound Planetary/Split Ring Compound Planetary - compound planet x3.stl
4.14 x 4.16 x 4.00

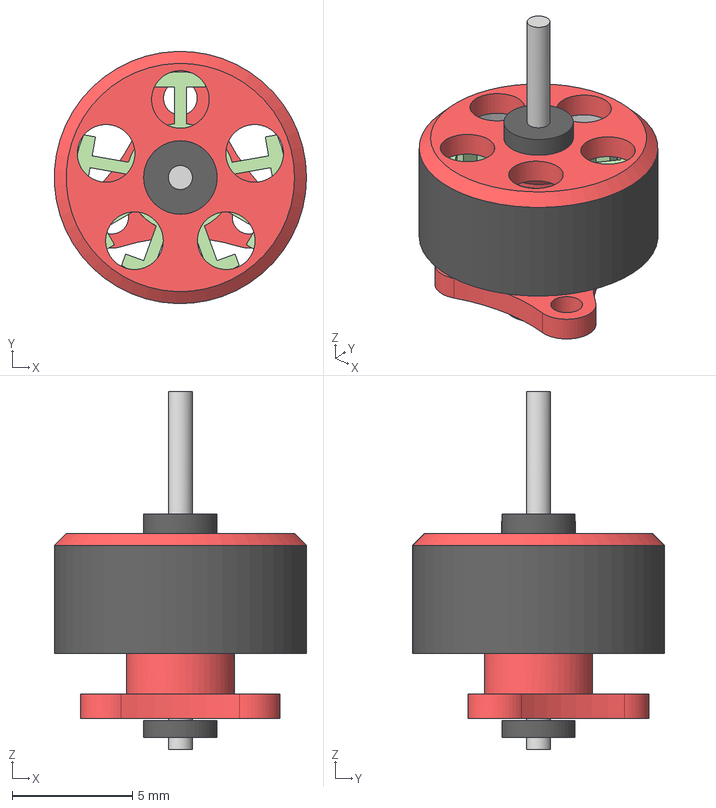
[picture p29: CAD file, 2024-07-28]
CAD/Electrical Parts/Happymodel SE0802.step
10.5 x 10.5 x 14.9 mm

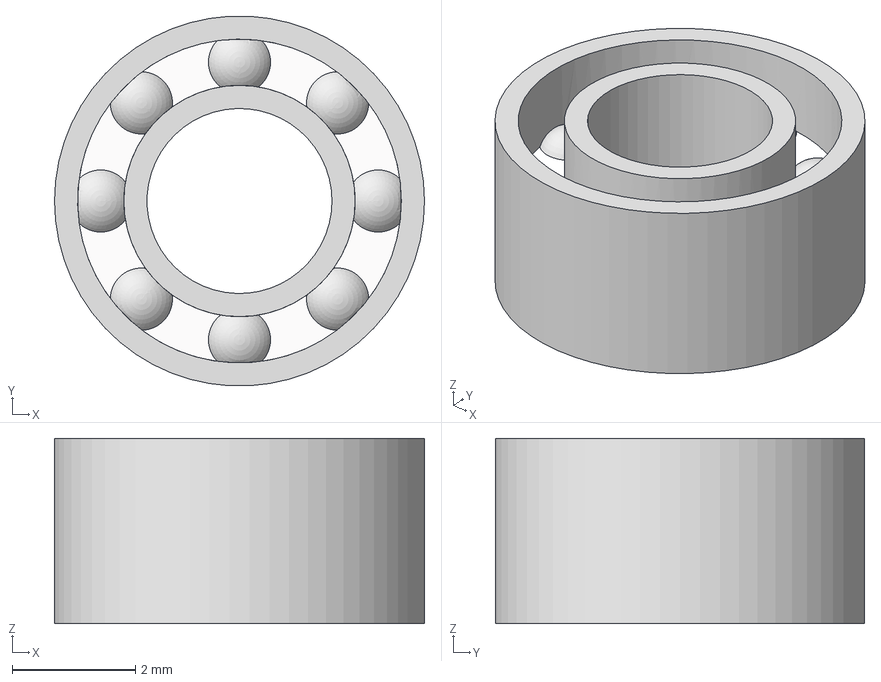
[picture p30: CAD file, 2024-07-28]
CAD/Mechanical Parts/Open Bearing.step
6.00 x 5.99 x 3.00 mm

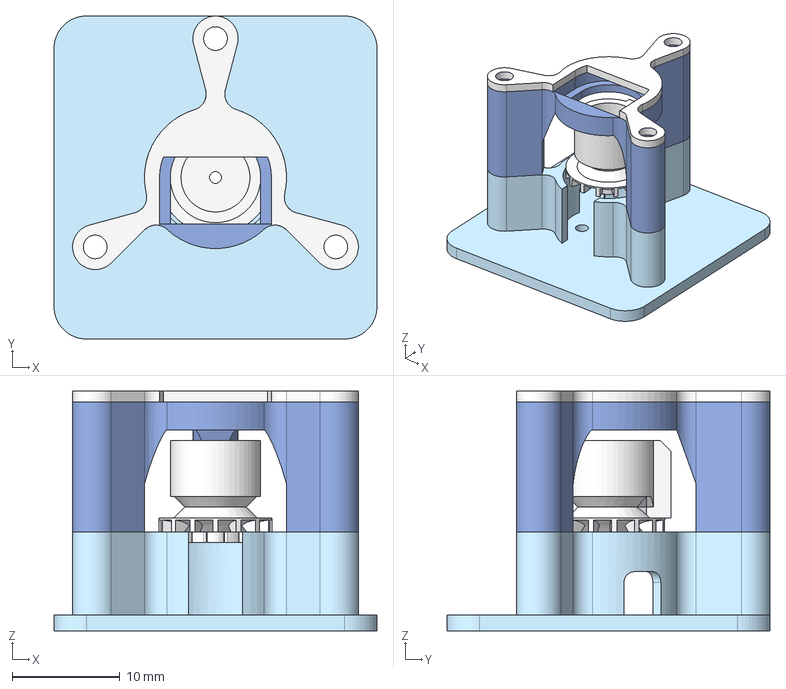
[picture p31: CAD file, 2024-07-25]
CAD/test magnetic encoder.step
30.0 x 30.0 x 22.3 mm

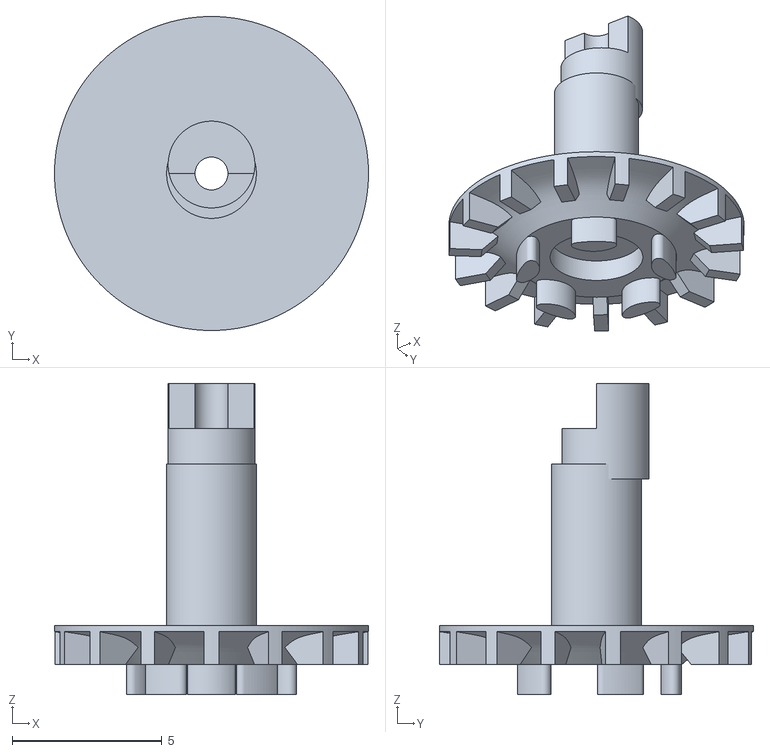
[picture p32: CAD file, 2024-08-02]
Print files/Cycloidal/Cycloidal - center shaft bottom.stl
10.5 x 10.5 x 10.4

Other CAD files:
Print files/Small Bearing x7.stl
Print files/Split Ring Compound Planetary/Split Ring Compound Planetary - 2nd stage output.stl
CAD/Mechanical Parts/Steel Rod.step
CAD/Test Gearboxes/Planetary.step
CAD/Test Gearboxes/Cycloidal No Bearings.step
CAD/Test Gearboxes/Cycloidal.step
Print files/Cycloidal/Cycloidal - 1st disk.stl
Print files/Cycloidal/Cycloidal - 2nd disc.stl
Print files/Cycloidal/Cycloidal - center shaft top.stl
Print files/Cycloidal/Cycloidal - motor mount.stl
Print files/Cycloidal/Cycloidal - output disc.stl
Print files/Cycloidal/Cycloidal - top cover.stl
Print files/Split Ring Compound Planetary/Split Ring Compound Planetary - 2nd stage sun.stl
Print files/Split Ring Compound Planetary/Split Ring Compound Planetary - base gearbox plate.stl
Print files/Split Ring Compound Planetary/Split Ring Compound Planetary - carrier.stl
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

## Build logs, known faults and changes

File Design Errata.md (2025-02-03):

# stm32g070 and DRV8311 single motor board - V1 Alpha

- Since I'm using 3x pwm mode for the driver, I should have tied the unused lowside pins to 3.3v, and not left them floating, according to the datasheet. To fix on my board, I have to solder a little wire to several leads on the QFN package, which is a hassle.
- I bought the wrong mosfets, which ended up being way to small for the footprint. I had a bodge fix put in place. Fixed in commit #f2471eab10ce7c932bcc07bac4c89c711445ac51
- The Nmos transistors do not work very well (besides size), and have a voltage drop of 0.6v!
- I can't get a 3.3volt power output from the driver chip on power-up, becauser there is a recursive design flaw. The driver chip has an enable pin with an internal weak pulldown. I put a pull-up resistor on the outside, to always keep the chip on. Guess what that is connected to though? The regulator output from the chip, which is disabled! :skull: I can however jumpstart this if I supply an external 3.3 volts, and then remove it.
- The LED circuit initially was designed for a tri-state, however the status indicator on the driver chip is not a tri-state. I fixed this in commit #f2471eab10ce7c932bcc07bac4c89c711445ac51, and only have the highside LED to indicated charging.
- LED resistor values were found last minute, and were not correct in the design. Fixed in commit #f2471eab10ce7c932bcc07bac4c89c711445ac51
- The 220uF aluminum capacitor is the wrong size, but still manages to work. The 220uF surface mount capacitor in design does not have a real life counterpart.

# esp32-s3 single motor & battery controller

- The polarity is swapped on the Balance charger plug, the positive wire on my turnagy batteries is the left one.
- I forgot to add a series resistor on the 40mhz crystal.
- There is a 10**thousand** ohm resistor on the VCC pin for the charger chip, limiting the current to 0.9 milliamps and effectively crippling the chip. It should have been a 10 ohm resistor to limit spikes.
- I have a redundant input current rush limiter circuit on VCC and on the adaptor input.
- The small mosfets have the wrong footprint, Sot323 instead of Sot23, meaning the part is  too large to fit on the pads.
- All the Mosfets have the wrong pin numbers assigned to them in the schematic! The large mosfets have source and drain swapped, and the small mosfets have gate and drain swapped
- I have one capacitor that was supposed to be on the current sense line instead being on the charger input line. It will be noisy!
- The i2c lines are crossing a ground plane split, and are going right near noisy components!

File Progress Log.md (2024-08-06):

# Progress Log
This is where I document my progress with pictures if I'm building something, or a description of what I did if I'm coding.

## July 1st, 2024
Today I assembled the bottom side of my control board.

**Setup:**

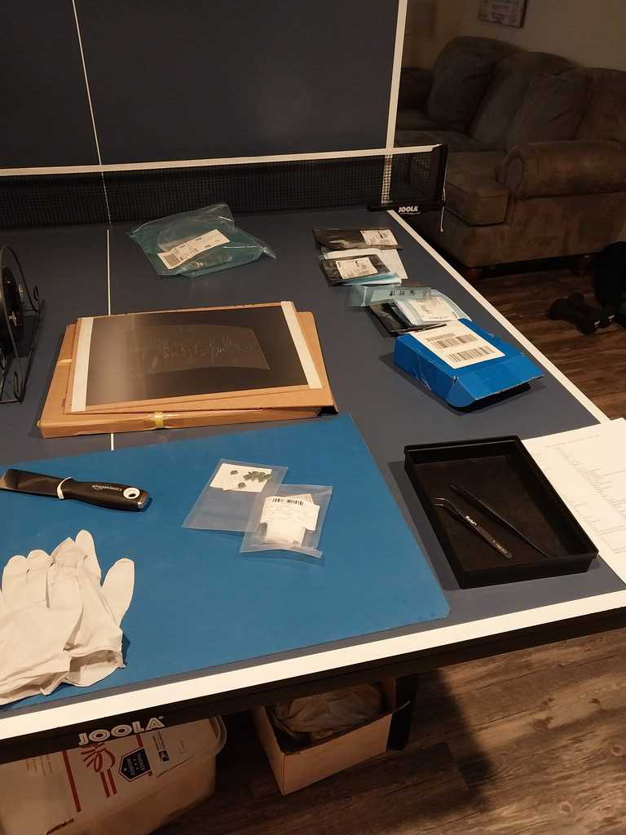
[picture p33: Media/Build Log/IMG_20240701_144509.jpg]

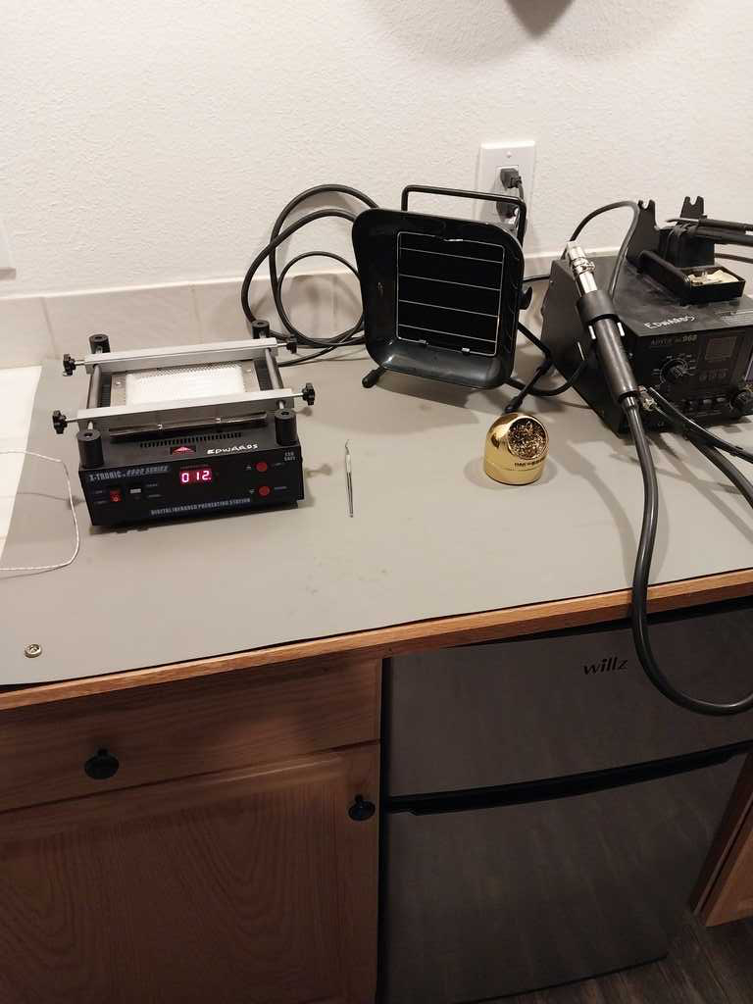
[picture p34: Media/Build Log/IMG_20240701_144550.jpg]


**Pasting**

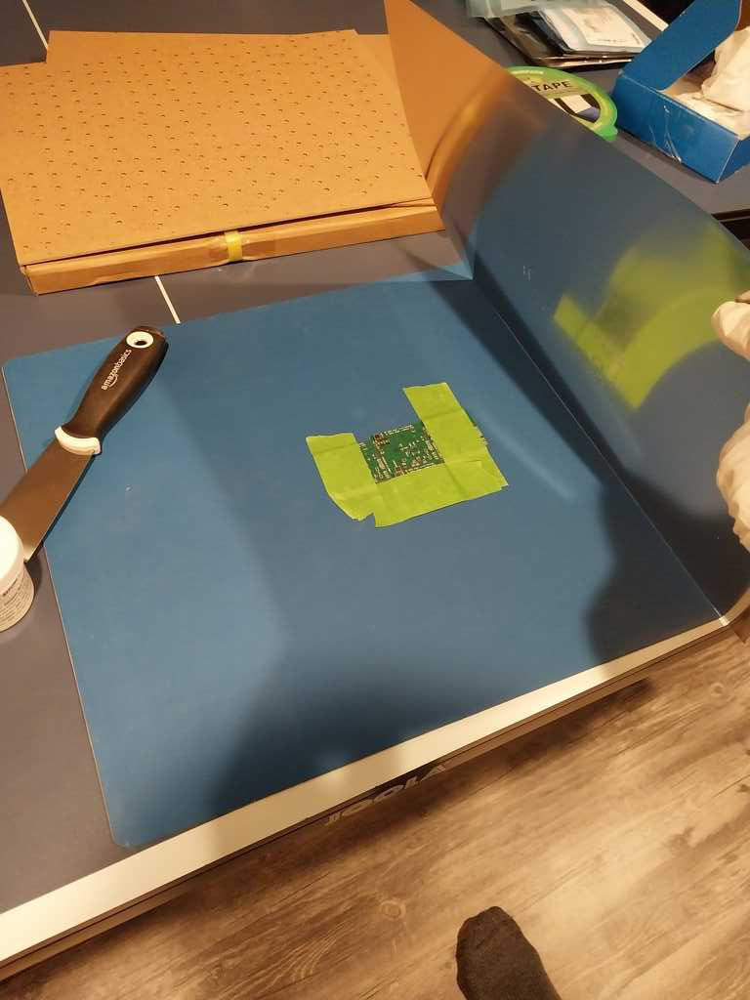
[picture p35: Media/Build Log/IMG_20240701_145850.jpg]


Got all the capacitors on the bottom

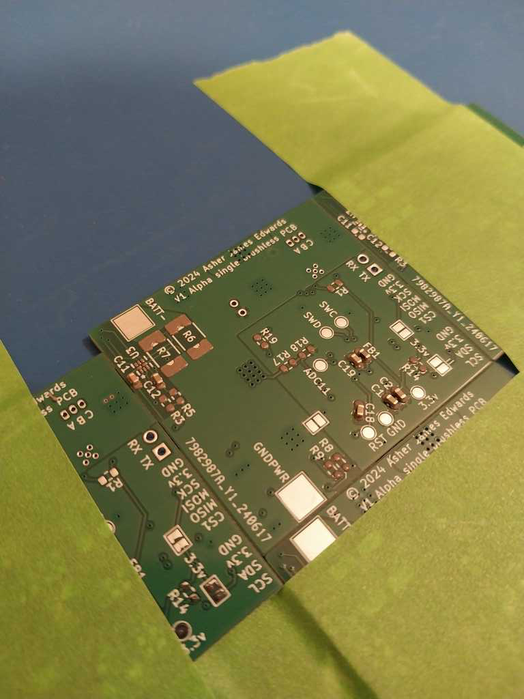
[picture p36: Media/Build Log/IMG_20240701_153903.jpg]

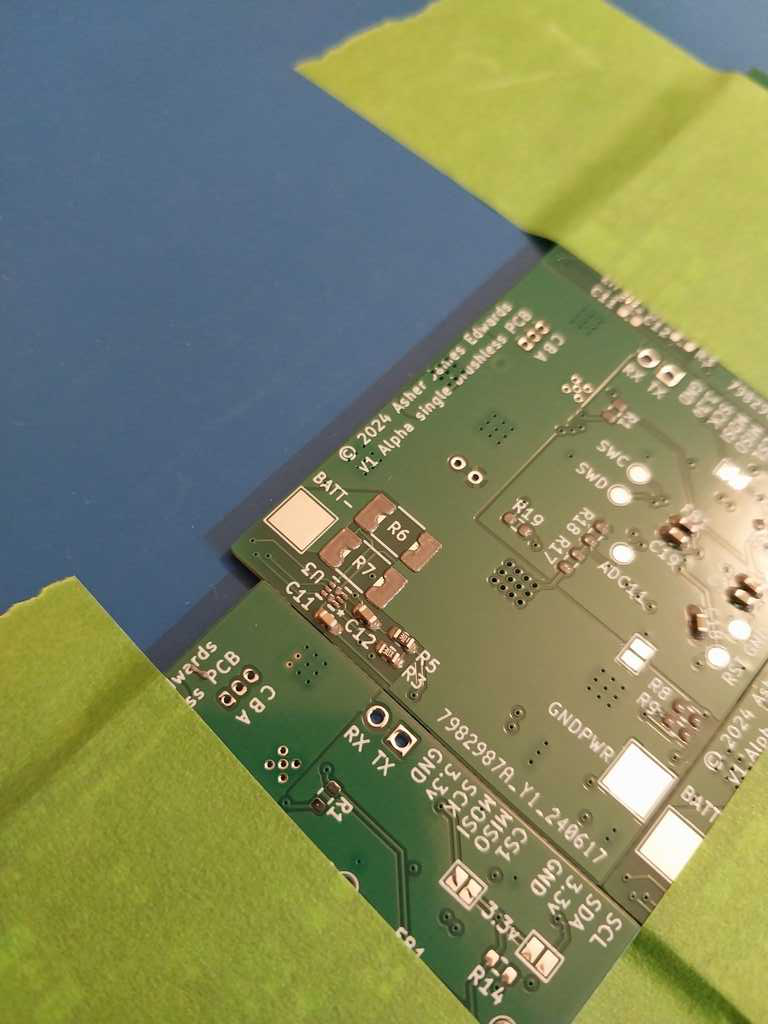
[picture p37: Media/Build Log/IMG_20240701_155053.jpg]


Added all the resistors

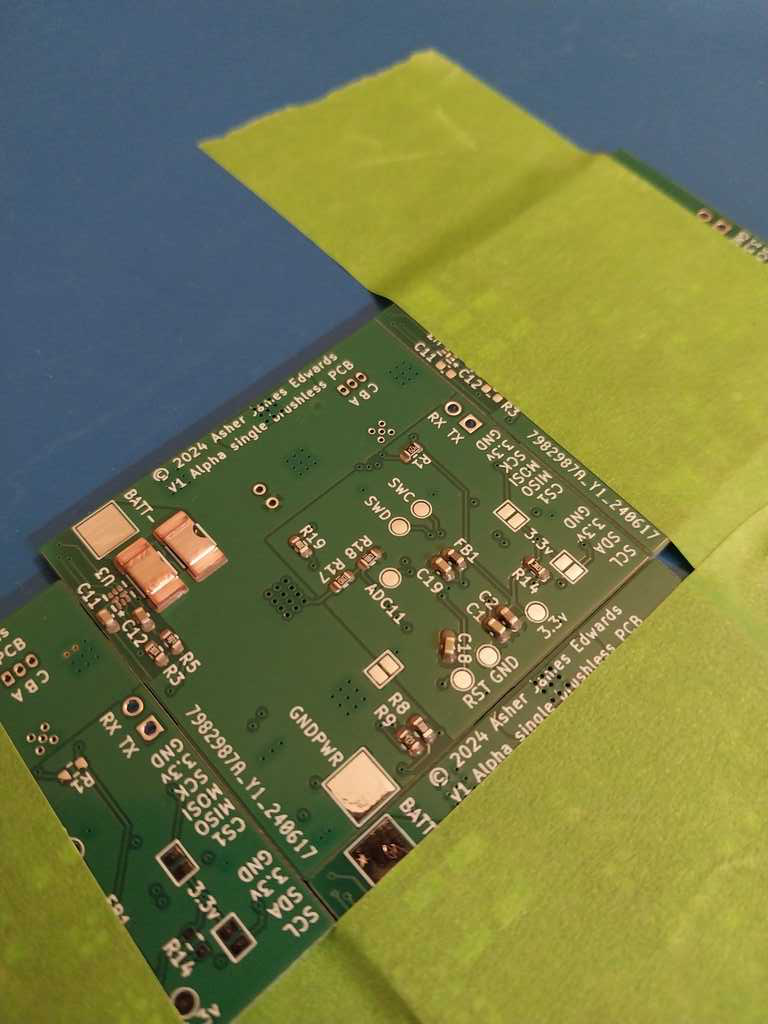
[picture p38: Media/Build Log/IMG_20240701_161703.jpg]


I had to place the battery protection IC using a microscope cause it's so tiny!

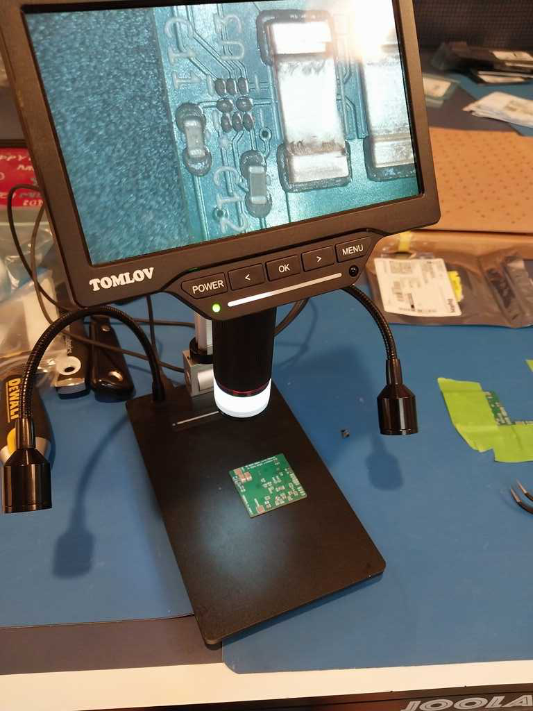
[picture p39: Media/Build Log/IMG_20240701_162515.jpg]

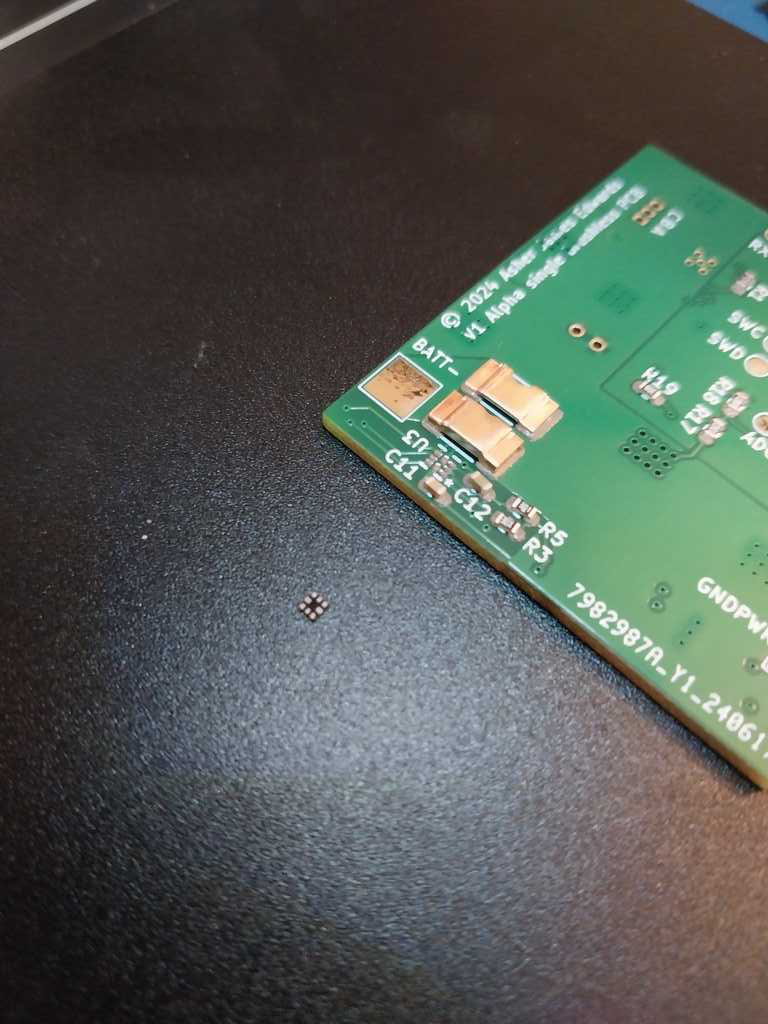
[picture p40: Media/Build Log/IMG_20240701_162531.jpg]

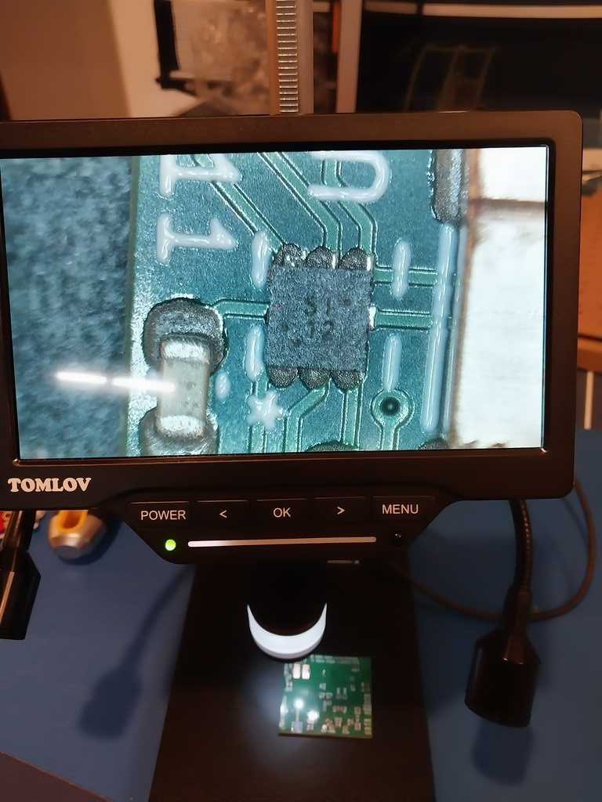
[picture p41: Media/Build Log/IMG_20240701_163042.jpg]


Reflowing

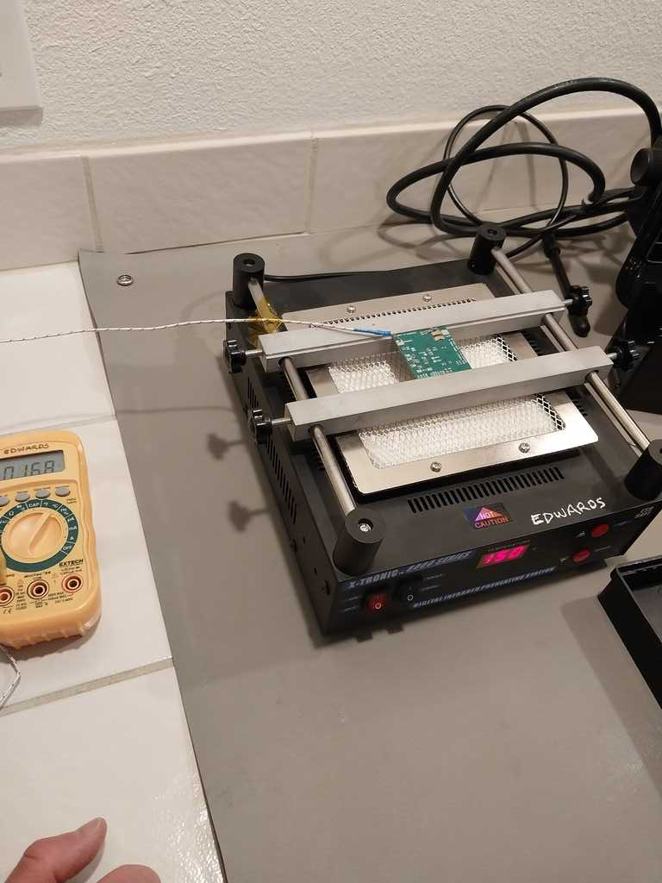
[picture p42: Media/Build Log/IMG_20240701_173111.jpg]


Finished the bottom, so I moved on to inspecting under the microscope and testing for shorts.

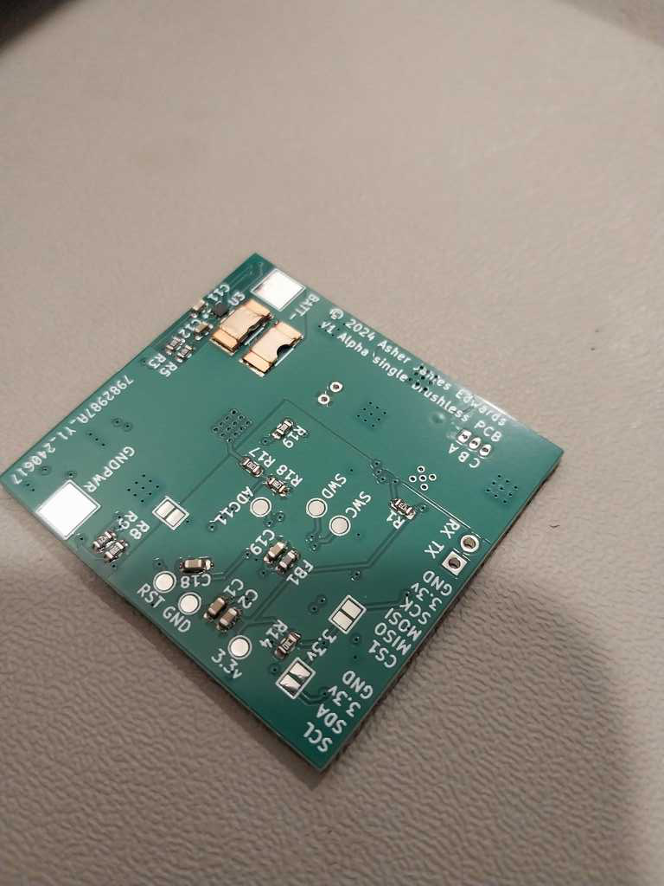
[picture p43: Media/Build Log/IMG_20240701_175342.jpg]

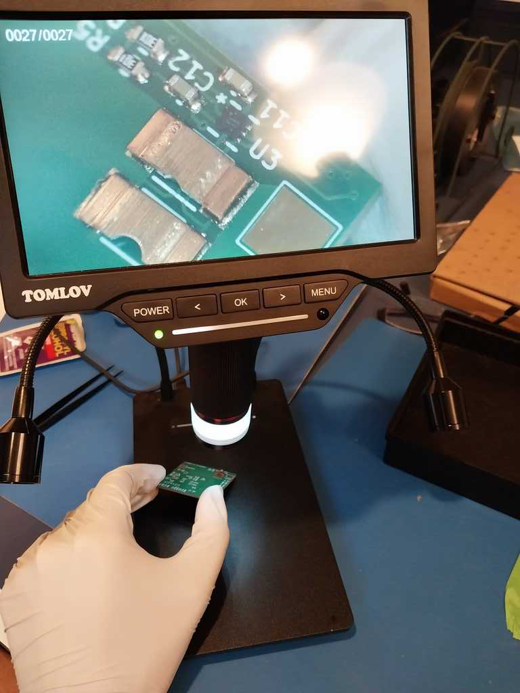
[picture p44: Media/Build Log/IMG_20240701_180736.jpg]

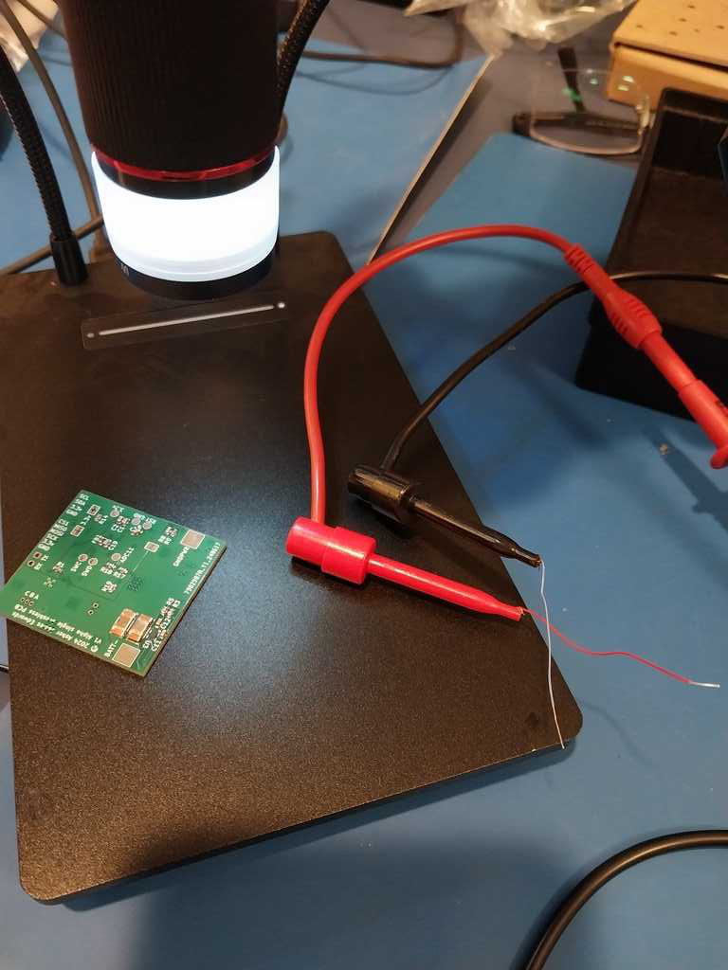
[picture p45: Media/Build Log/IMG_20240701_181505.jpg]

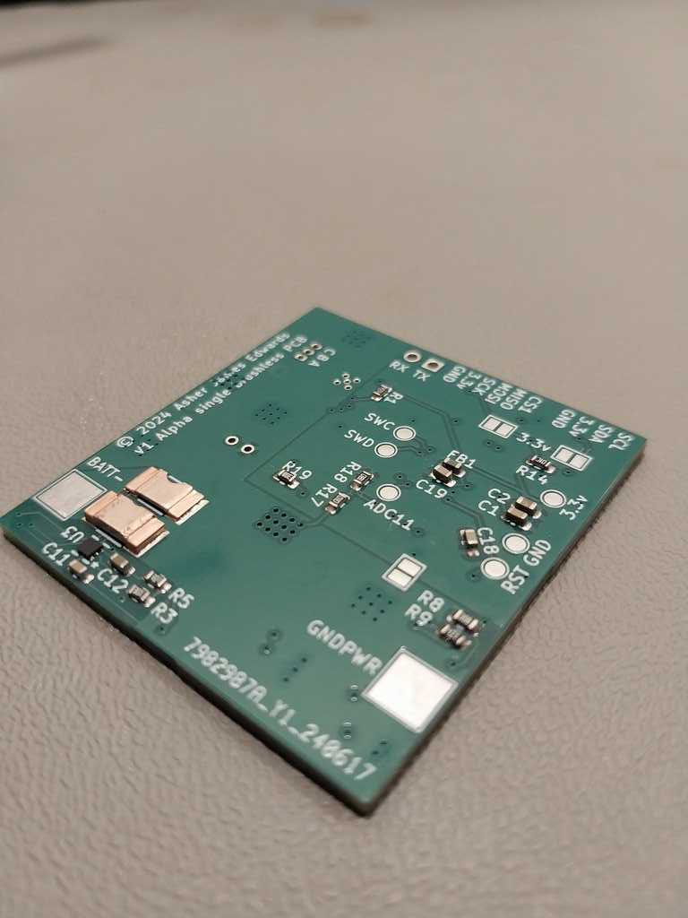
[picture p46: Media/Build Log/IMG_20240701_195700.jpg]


## July 2nd, 2024
Today I assembled the top side of my control board, as well as the encoder board.

Pasting

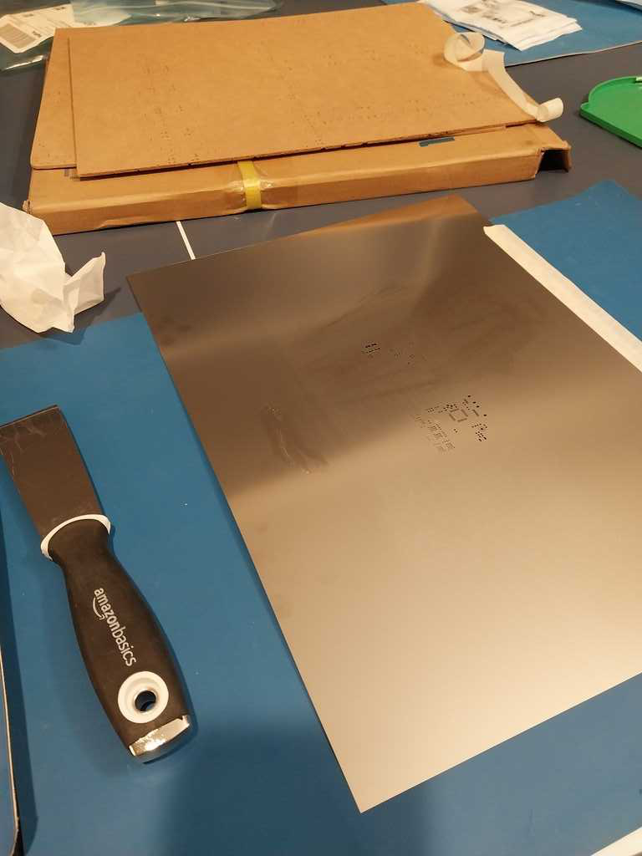
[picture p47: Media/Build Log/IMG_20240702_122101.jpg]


The layer is a bit thick, but it should work

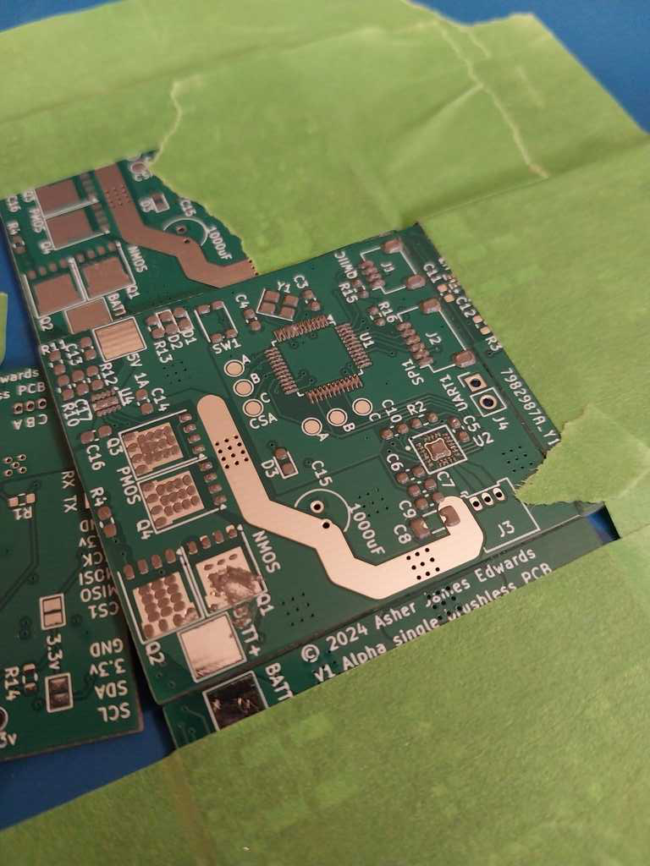
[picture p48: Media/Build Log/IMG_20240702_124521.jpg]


Added all the capacitors

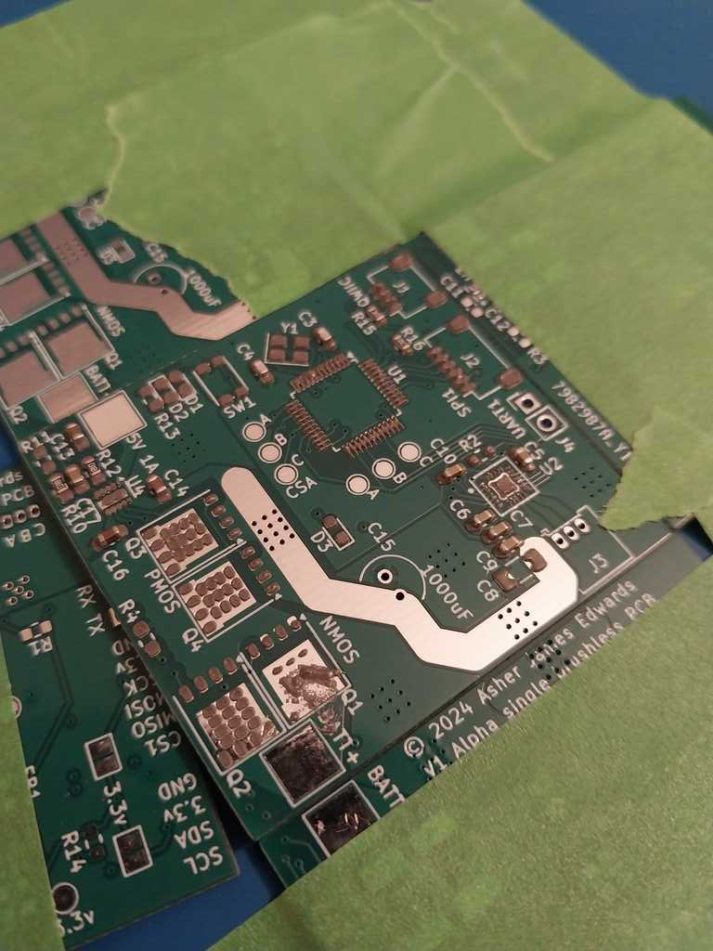
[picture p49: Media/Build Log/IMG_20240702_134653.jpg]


Added all the resistors

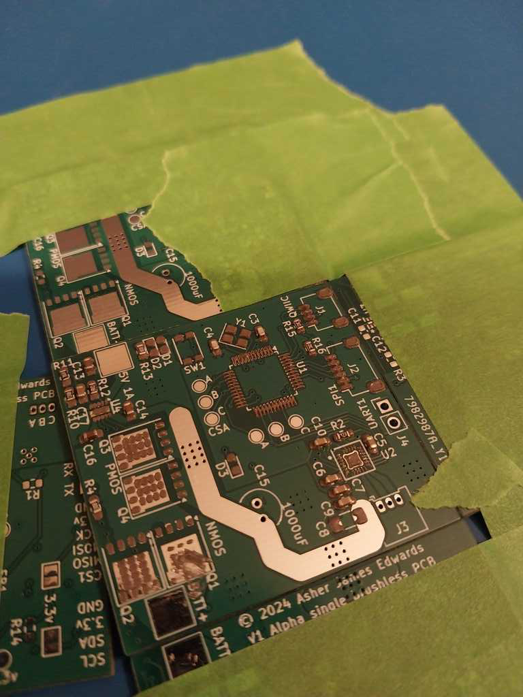
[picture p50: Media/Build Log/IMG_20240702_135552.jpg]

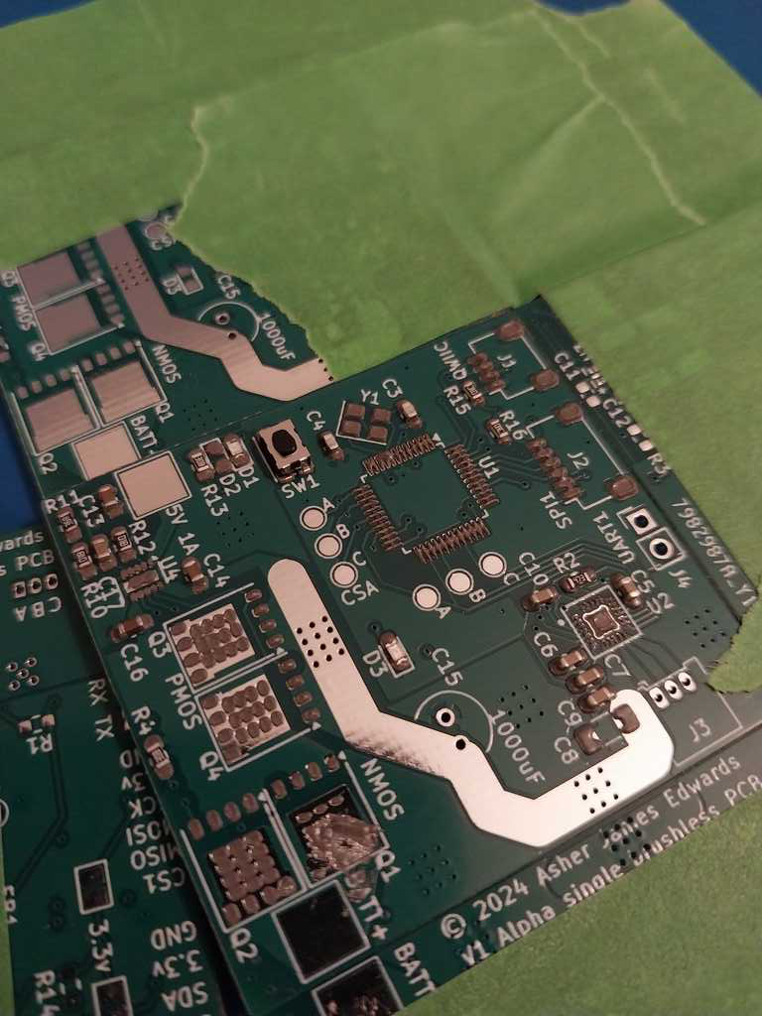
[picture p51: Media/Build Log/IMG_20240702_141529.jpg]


Started adding ICs

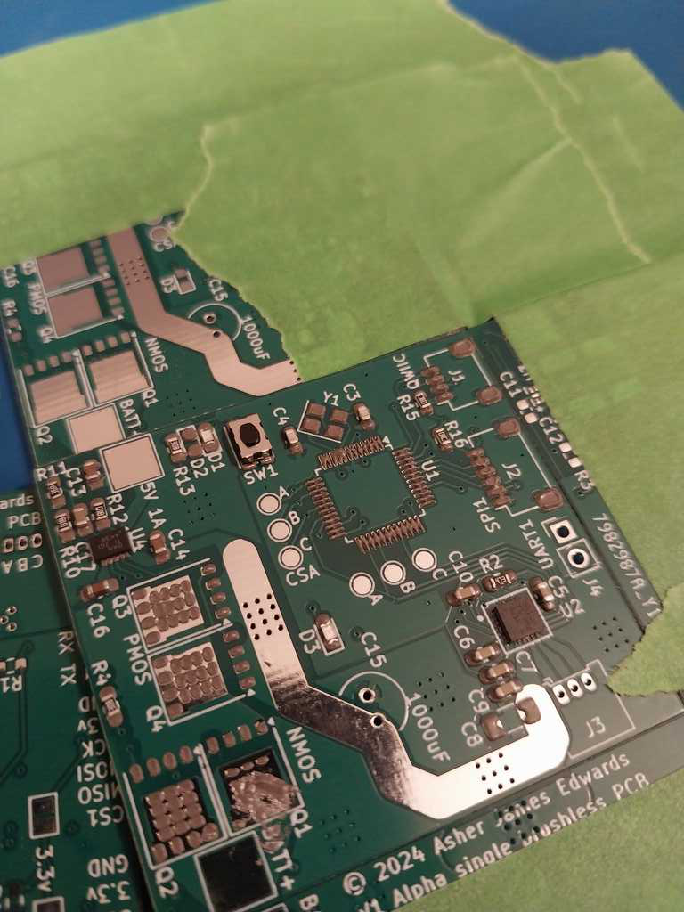
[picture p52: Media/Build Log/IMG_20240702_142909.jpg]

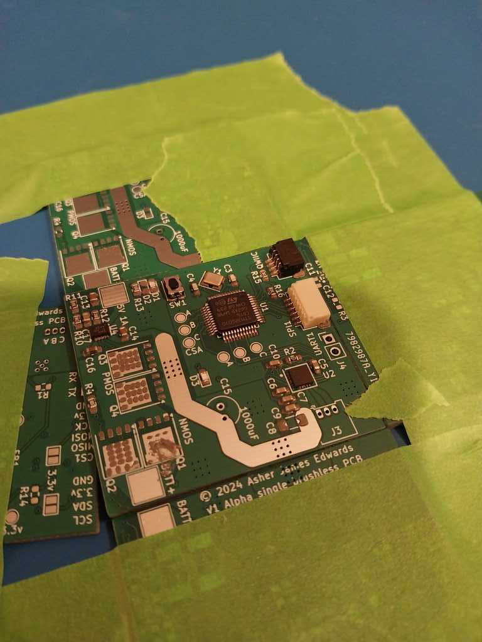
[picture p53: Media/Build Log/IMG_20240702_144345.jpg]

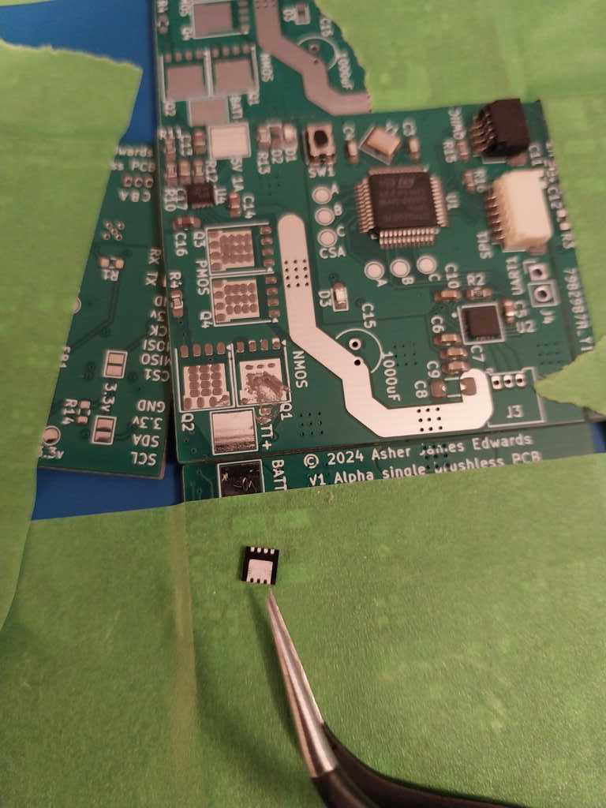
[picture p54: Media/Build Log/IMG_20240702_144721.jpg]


I realized at this point I bought the wrong mosfet package size. I had an idea for a quick fix though.

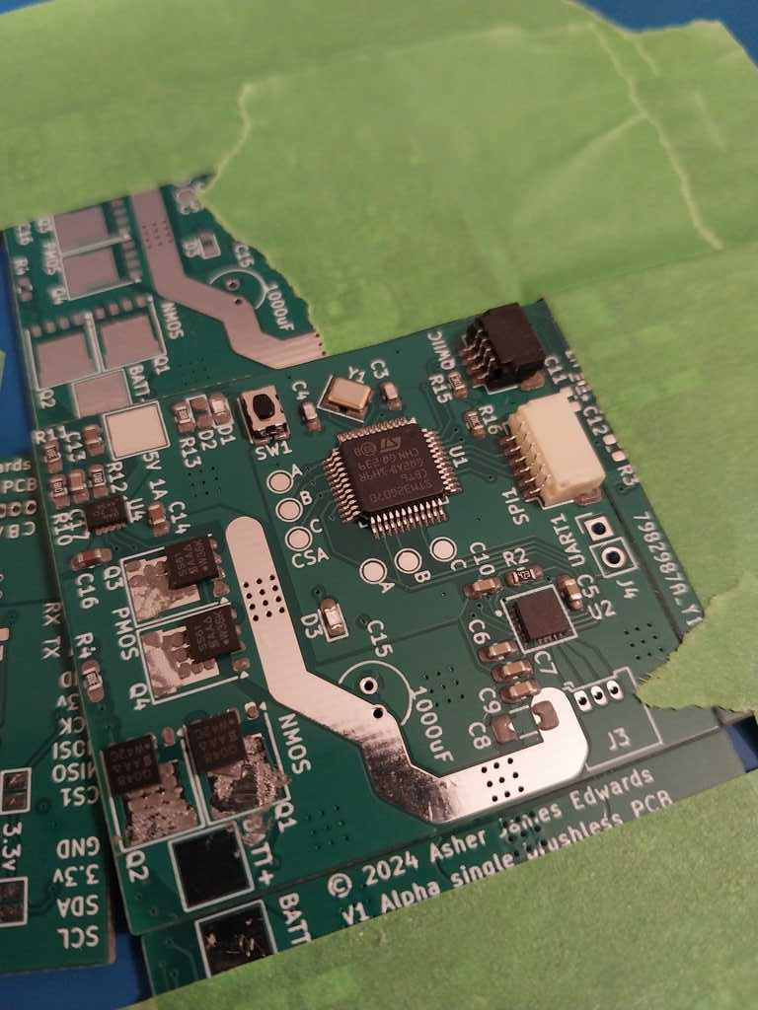
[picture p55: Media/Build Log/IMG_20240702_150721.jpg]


Reflow

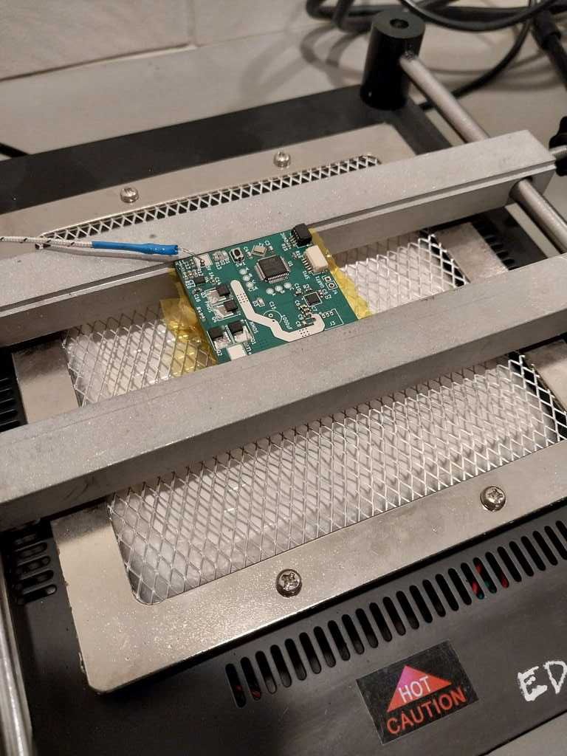
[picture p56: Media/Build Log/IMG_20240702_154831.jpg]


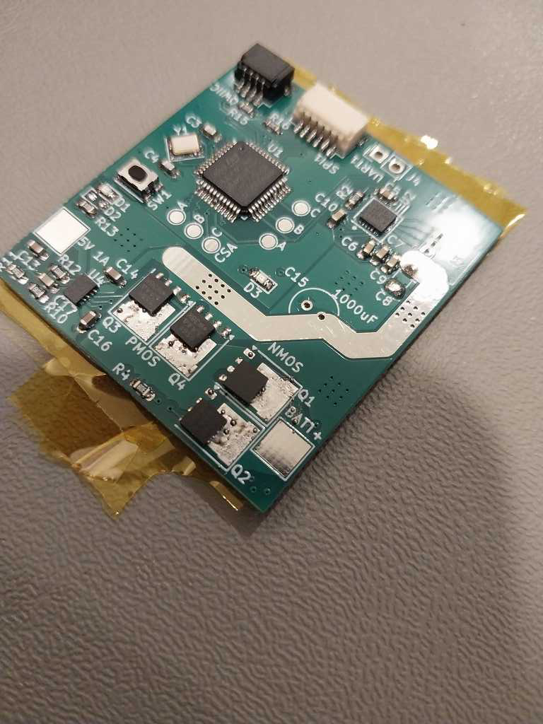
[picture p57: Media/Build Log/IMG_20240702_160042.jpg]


Inspecting. There is definitely too much solder

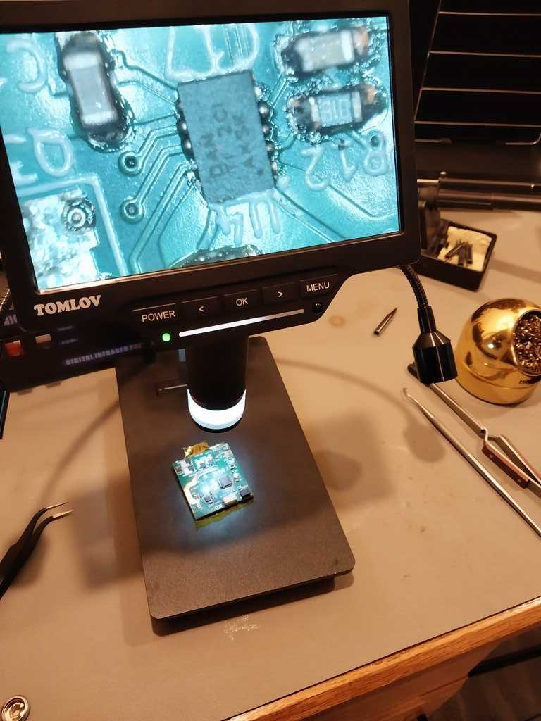
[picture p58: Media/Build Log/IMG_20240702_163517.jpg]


Had to add some extra solder on the mosfets.

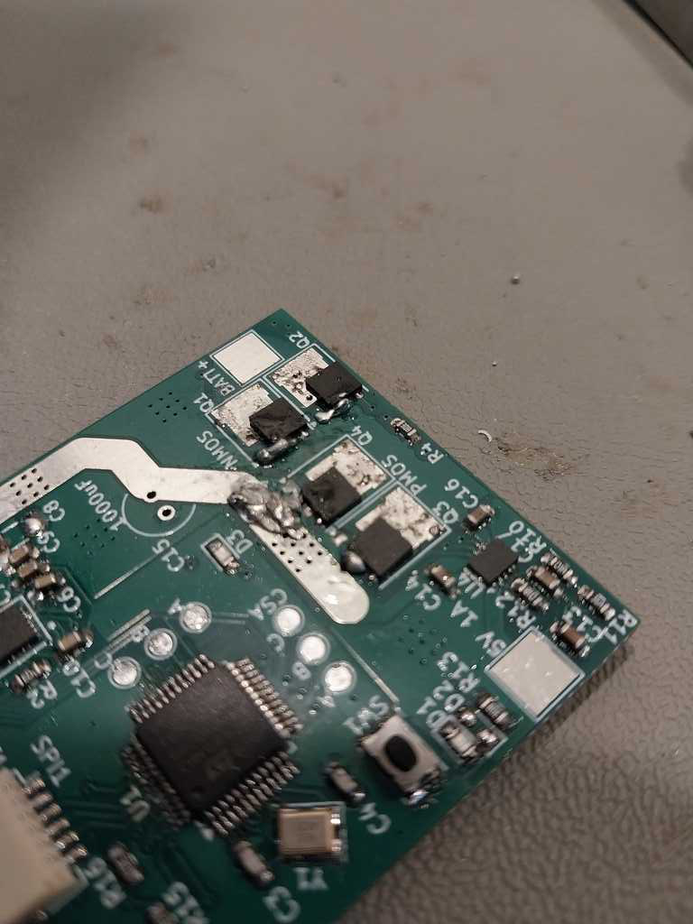
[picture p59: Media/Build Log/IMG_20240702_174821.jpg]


I realized I put the wrong resistors down for the leds, so I replaced them.

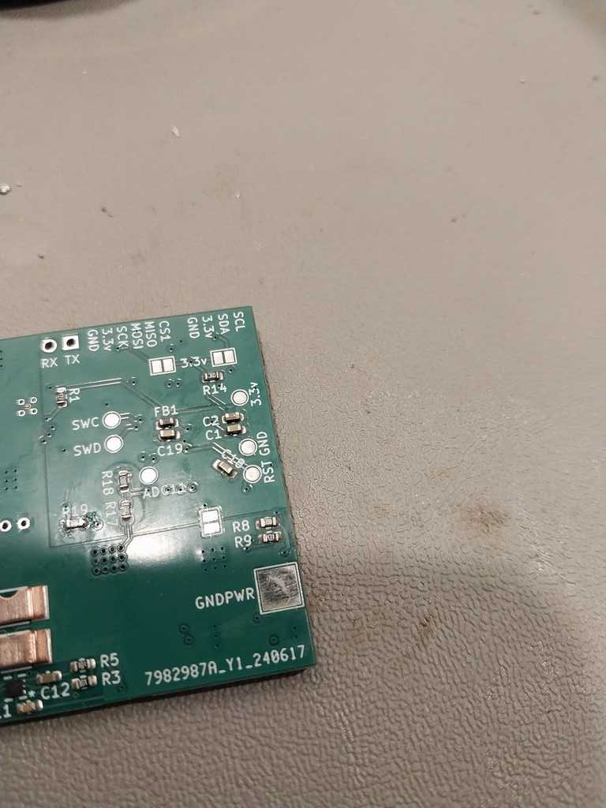
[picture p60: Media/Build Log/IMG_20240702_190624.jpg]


The big capacitor wouldn't solder to the ground plane, so I'm heating the board up to make it easier

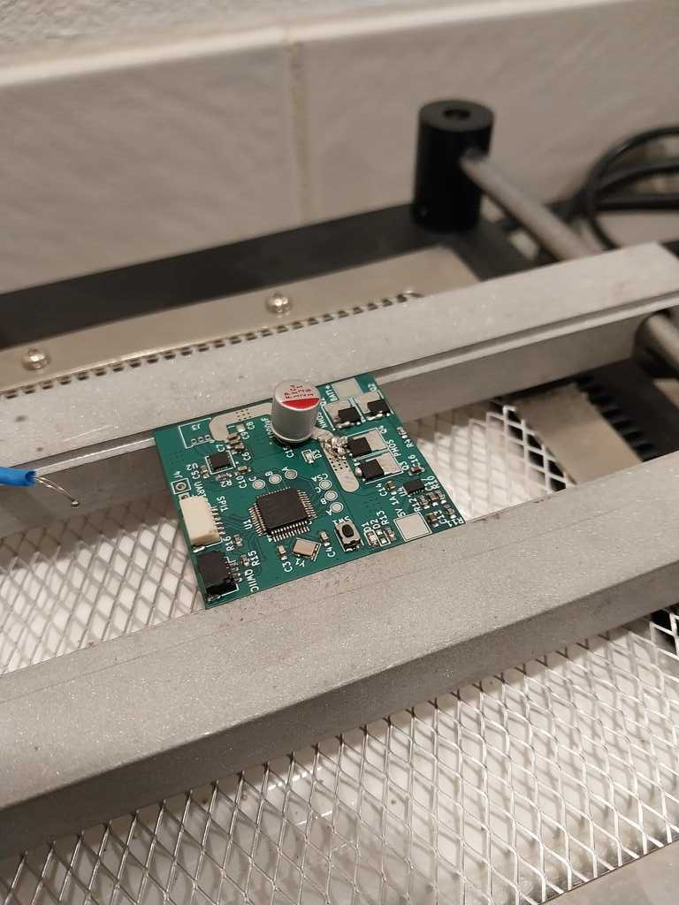
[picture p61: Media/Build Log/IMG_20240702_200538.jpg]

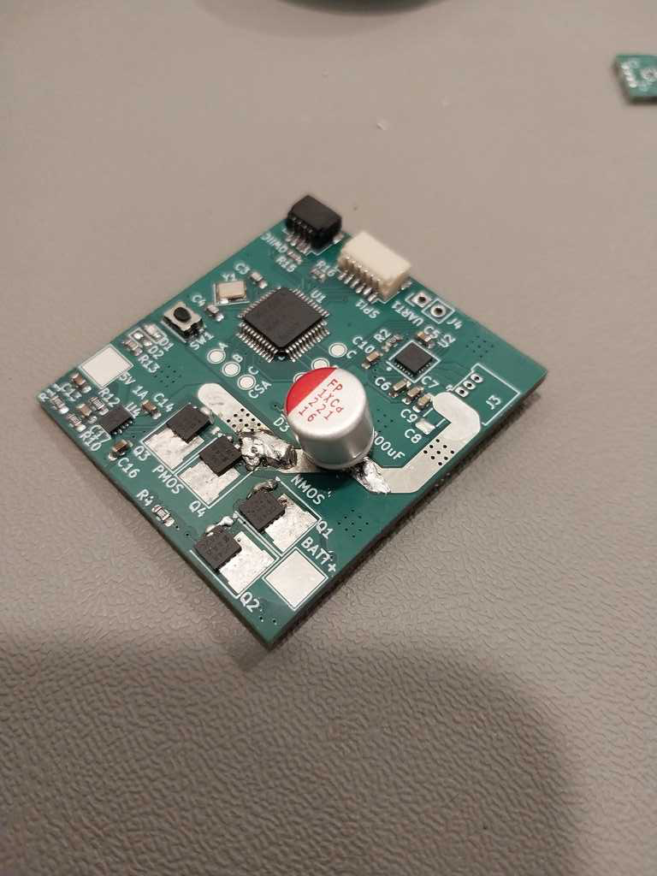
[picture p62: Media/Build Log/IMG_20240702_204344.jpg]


Doing the magnetic encoder board here.








## July 3rd, 2024
Today I am mostly soldering wires to the test points and the power inputs.








Accidentally misplaced a component



Fixed it now.




All ready for blast testing!



It did not blow up when I applied power, but unfortunately it didn't do anything. For some reason the power protection chip is failing and not opening up the mosfets. I tested manually by appling a small current to the mosfets, which opened up and let power through the whole board. I think I will have to bypass the circuit to continue testing, because visually I don't see anything wrong. There may be a short hidden underneath the chip, or the chip may be faulty.

## July 5th, 2024

I spent most of my afternoon debugging. I have identified two more design flaws. Since I'm using 3x pwm mode for the driver, I should have tied the unused pins to 3.3v, and not left them floating! I found this in the datasheet. To fix on my board, I have to solder a little wire to several leads on the QFN package, which is a hassle. I also can't get a 3.3volt power output from the driver chip, and discovered a recursive design flaw causing this. The driver chip has an enable pin with an internal weak pulldown. I put a pull-up resistor on the outside, to always keep the chip on. Guess what that is connected to though? The regulator output from the chip, which is disabled! :skull:

BTW I added a file for [Design Errata](Design%20Errata.md)

## July 6th, 2024

I managed to solder on the very difficult bodge wire needed to the QFN chip. This ties the three lowside drive pins to 3.3 volts



I also fixed the design errors I identified yesterday in the kicad files.

## July 7th, 2024

I finally figured out how to add custom programmers to arduino IDE! I wanted to use my Flipper zero with the DAP-link application to program my board, so I looked through the arduino manual and through some of the other programmers to figure out how to do it. There is a file called `programmers.txt` in every installed boards file definition, which in my case was in `.arduino15/packages/STMicroelectronics/hardware/stm32/2.8.0/` (I installed stm32 support from https://github.com/stm32duino/BoardManagerFiles/raw/main/package_stmicroelectronics_index.json) The only supported programmer was the stlink, so I added my own flipper zero support using openocd like I found in other examples:

```txt
flipper.name=Flipper Zero DAP-link
flipper.communication=USB
flipper.protocol=cmsis-dap.cfg
flipper.program.tool=openocd
flipper.program.tool.default=openocd
flipper.extra_params=-c "transport select swd"
flipper.extra_params=-c "adapter speed 9600"
```

I had to delete `.config/arduino-ide` for it to actually show up, because there were temporary files stored there. This may be different depending on platform, see https://support.arduino.cc/hc/en-us/articles/4415103213714-Find-sketches-libraries-board-cores-and-other-files-on-your-computer User Data folder.

I was finally able to program the basic Blink.ino! It works!

Now I'm trying to setup the clock usage. For some reason my blink code is taking up 40k bytes! Over head with absolutely no code is around 4.6k. The clock settings appear to get the clock to around 32 mhz, not 64. I think I set the wrong clock divisor...

I also tried to setup serial out to print hello world. I failed at wiring several times, but finally got it to print gibberish (Which means the baud rate is wrong). For some reason the serial baud rate on the computer has to be twice that what was configured in code. Clock issues?

I eventually worked it out. I had to specify in `hal_conf_extra.h` this: `#define HSE_VALUE    (16000000UL)` This told the compiler what the external clock frequency I was using. After that I had no serial timing issues and got the full 64mhz.

## July 16th, 2024

Today I finished out the basic hardware testing (except the battery charging, I don't have a battery yet), and moved on to setting up SimpleFOC. I have verified that the digital pins work, and the SPI interface works.

I also started work on a custom MA735 library, to work with the specific registers

## July 17th, 2024

I finished MA735 driver support, so now I can set resolution or update time. I can of course read the position of the magnet.

I also started work on motor setup.

I had to measure resistance between two leads to calculate phase resistance, then divided by 2 since it is a Wye/star configuration. I pretty sure of the configuration since I see a little wire tail going nowhere.




Phase resistance ended up being 0.2 ohms! Really low, but that is to be expected.

My temporary motor mount:




It definitely unorthodox, but it works to hold the motor in place while running it. The prop guard shown here was for a motor twice the size. Soon, hopefully, I will have a gearbox setup 3D printed that will be long term.

## July 18th, 2024

I spent most of the day debugging the motor. Nothing was working. I did get an encoder mount though.


## July 19th, 2024

I finally found the fix! I tested the output pins and pin C was misbehaving, outputting double the frequency! This meant that my bodge fix was not connected to the lowside pin c. I spent two hours today trying to fix that.




It worked!

Another thing I discovered today was a bug in my code that cause sensor alignment to fail! I needed to call motor.init() AFTER all the config stuff, not inbetween!

## July 20-21, 2024

I tuned the velocity PID loop on the motor, reaching around 800 rad/s, or 7600 rpm. Its fast and loud, but nowhere near the rated motor speed. When its in openloop I can get to 1140 rad/s in little increments before the motor phases out. I'm wondering honestly if the MCU is the bottleneck, its only clocked at 64mhz and it doesn't have an FPU.

## July 22-24, 2024

I spent a few hours adding wires to my board to test out other MCUS to see if I could reach higher speeds. This is an adafruit feather with a stm32f405 processor, at 168mhz.


After tuning the FOC current control loop (something I couldn't do on the built in either) I was able to push the motor way higher than my previous limit! 2100rad/s, or 20k RPM!!!. I now have reached the manufacture limit value of 19kv, since I am running a 2.5 amp current limit at 1 volt, and have reached 20krpm. I tested again with the onbaord mcu, and it could only reach around 600rad/s.

I did some testing of instantanious motor speeds, and have concluded that 1,700 is the max speed it can go from a stand still.

## July 25-31, 2024

I designed a 16 to 1 cycloidal gearbox to go on my motor. Its rather complex.





## Aug 1-4, 2024
I have printed several revisions of the gearbox in resin, tweeking some tolerances and such. The parts are very fragile with the resin I have. I can't print engineering resin due to the more toxic fumes in my house, so I will have to outsource it when the time comes.




One thing to note is that I really did not plan very well in advance with the magnetic encoder board. I soldered all the wires before assemble, and didn't realize that I would have to feed the wires through the cycloidal disc. The base part has slots to insert the wires in after soldering, but the cycloidal disc is continous. I had to cut the disc to get the wires in. My next board revision will have a flex circuit with a built in FPC cable that can be fed through easily.

## Aug 5th, 2024

I finished my wiring diagram for the esp32, which I will eventually use in a 4 motor control board. It is really cramped, having almost no free pins except the strapped boot pins. 2 spi interfaces (sensor and command interface), four 3xpwm interfaces, four 2 pin current sense amplifier lines, and the rest of the reserved pins (4 strapped pins, 2 usb, 6 internal SPI). The supposed 48 gpio pins got eaten up pretty fast with unusable pins, and 4 motors.



 I also wired a dev board in realy life to my motor driver and tested.

The gearbox did not function at all, and I discovered the culprit. The whole base was too tight around the motor, causing friction. I could rotate it by hand without a ton of effort, but it was different, and clearly enough for the motor to not spin at all. I need to reprint and/or increase tolerance.

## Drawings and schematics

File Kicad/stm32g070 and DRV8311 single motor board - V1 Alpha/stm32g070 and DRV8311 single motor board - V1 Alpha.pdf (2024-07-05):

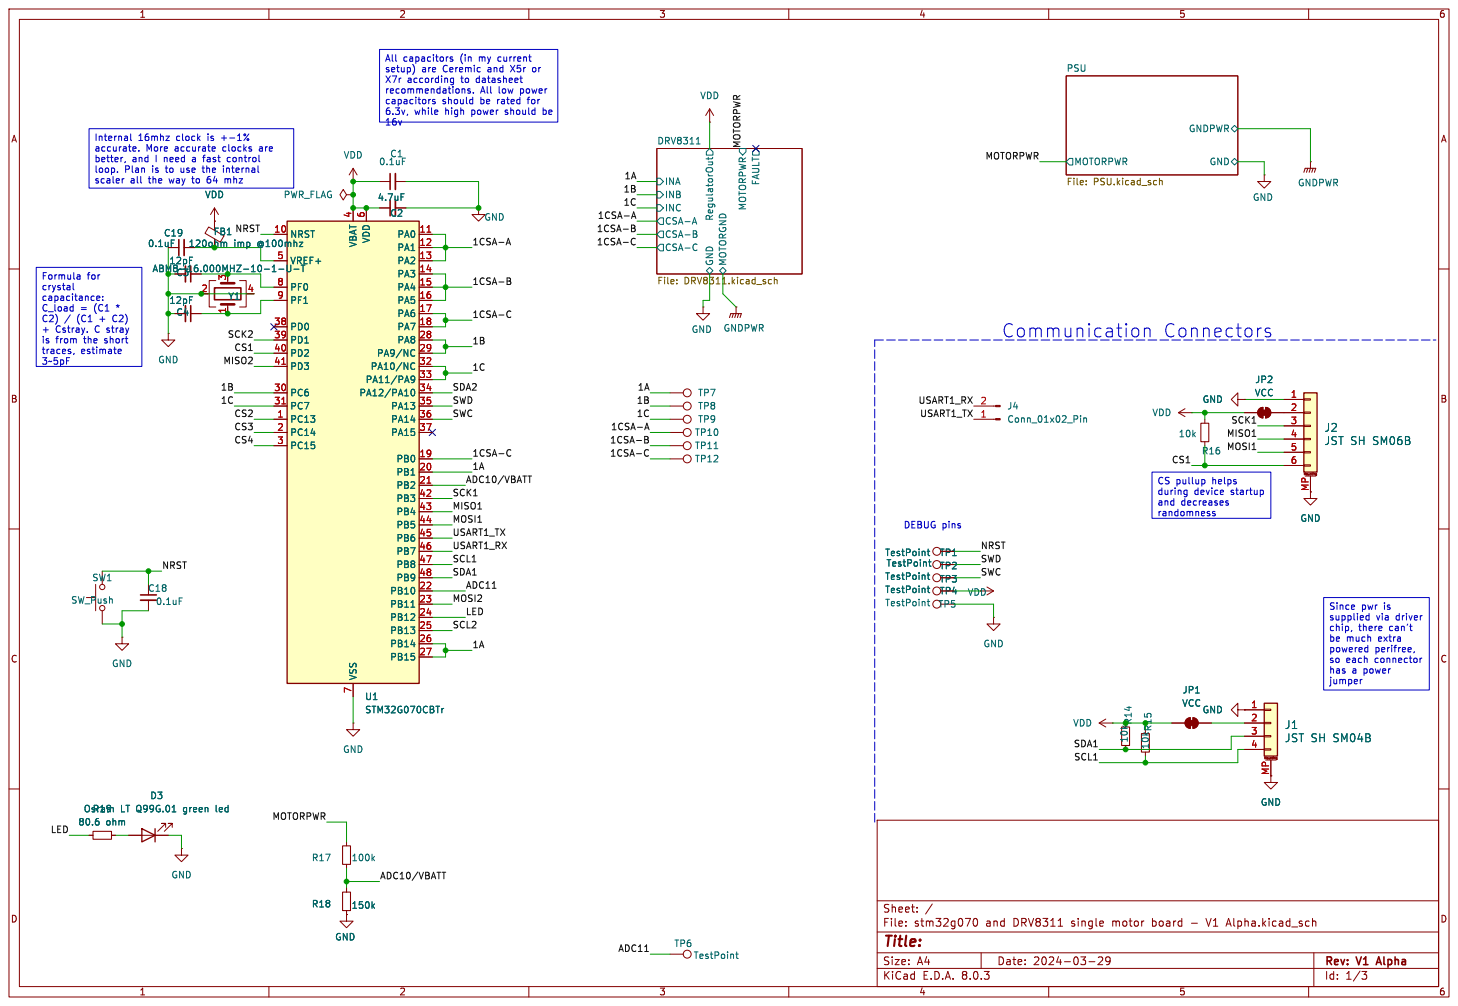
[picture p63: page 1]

better, and I need a fast control

loop. Plan is to use the internal scaler all the way to 64 mhz Formula for crystal

is from the short
traces, estimate

powered perifree, so each connector has a power

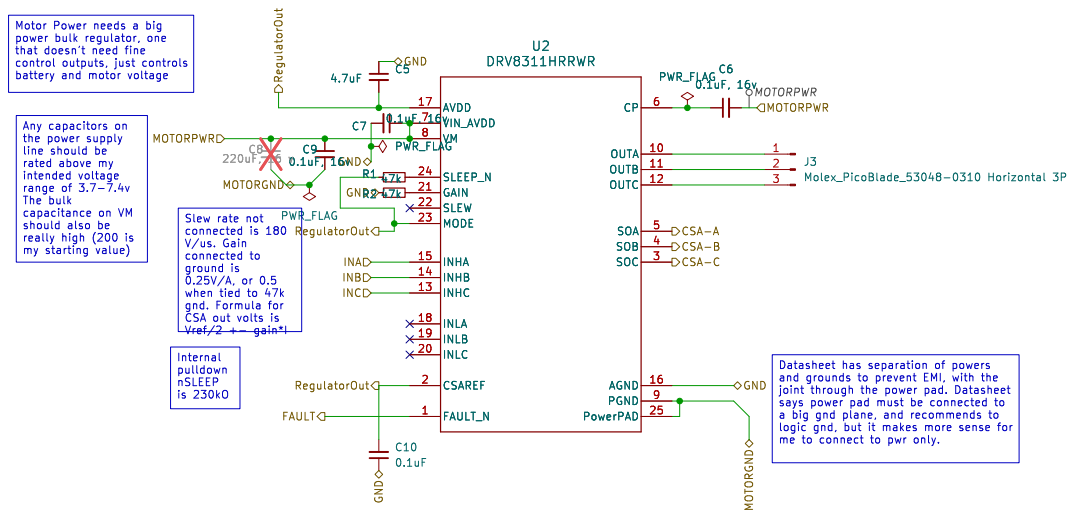
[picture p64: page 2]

that doesn't need fine

the power supply
line should be
rated above my
range of 3.7-7.4v The bulk

logic gnd, but it makes more sense for me to connect to pwr only.

Id: 2/3 Title: File: DRV8311.kicad_sch Sheet: /DRV8311/

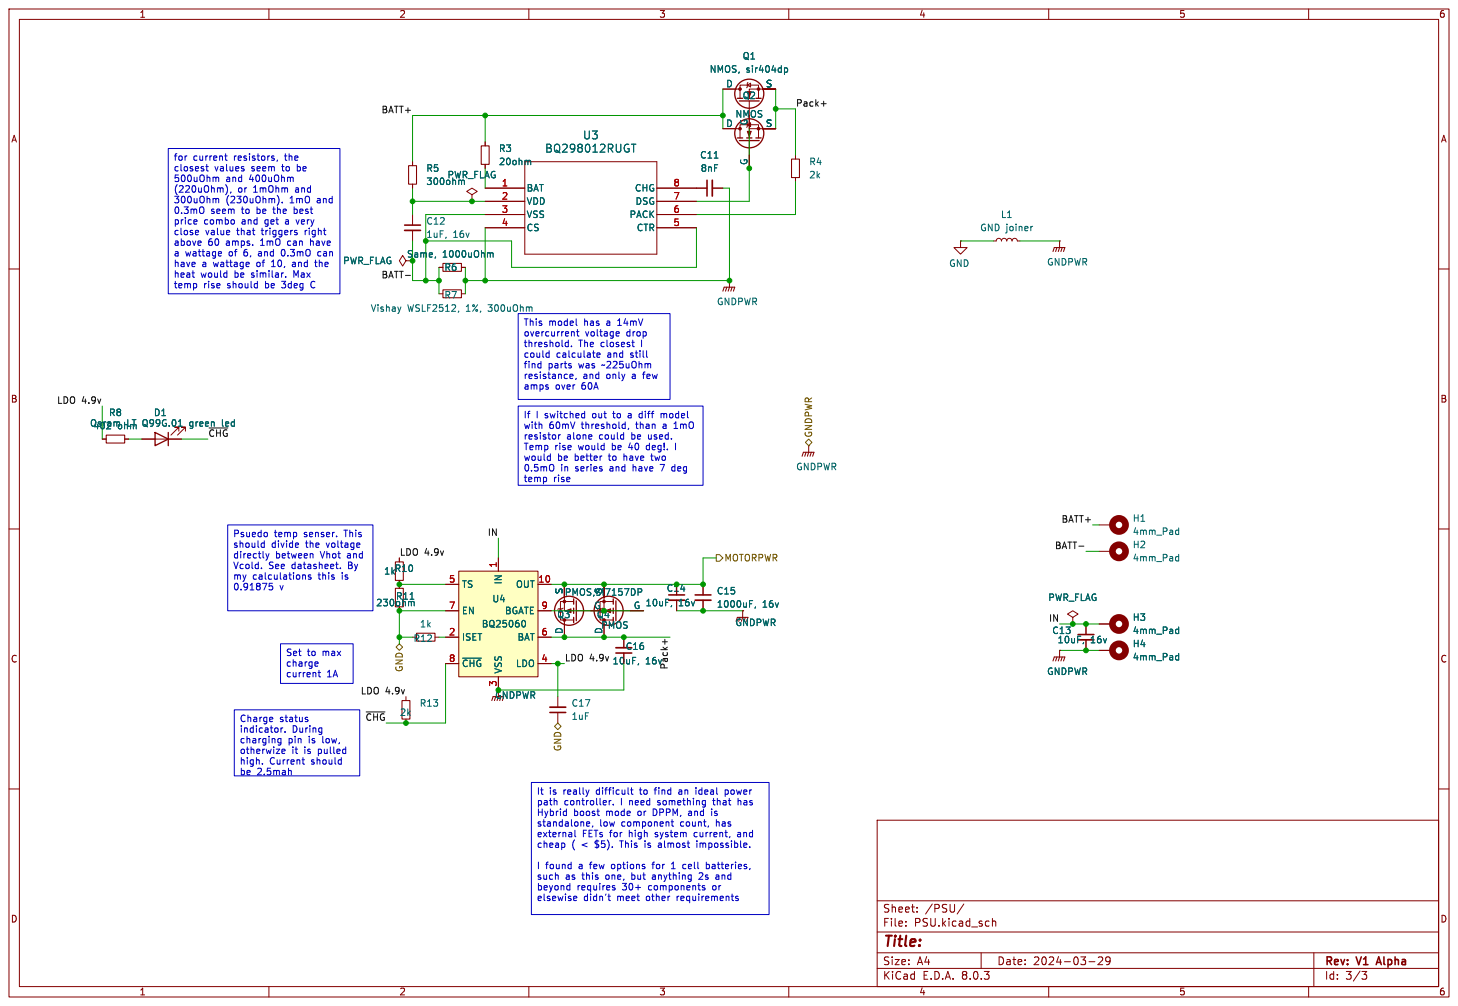
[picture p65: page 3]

closest values seem to be
500uOhm and 400uOhm
0.3mO seem to be the best price combo and get a very

a wattage of 6, and 0.3mO can
have a wattage of 10, and the
temp rise should be 3deg C

D Q4PMOS D1 Osram LT Q99G.01 green led GNDPWR
402 ohm

temp rise Psuedo temp senser. This

0.5mO in series and have 7 deg

should divide the voltage

cheap ( < $5). This is almost impossible.

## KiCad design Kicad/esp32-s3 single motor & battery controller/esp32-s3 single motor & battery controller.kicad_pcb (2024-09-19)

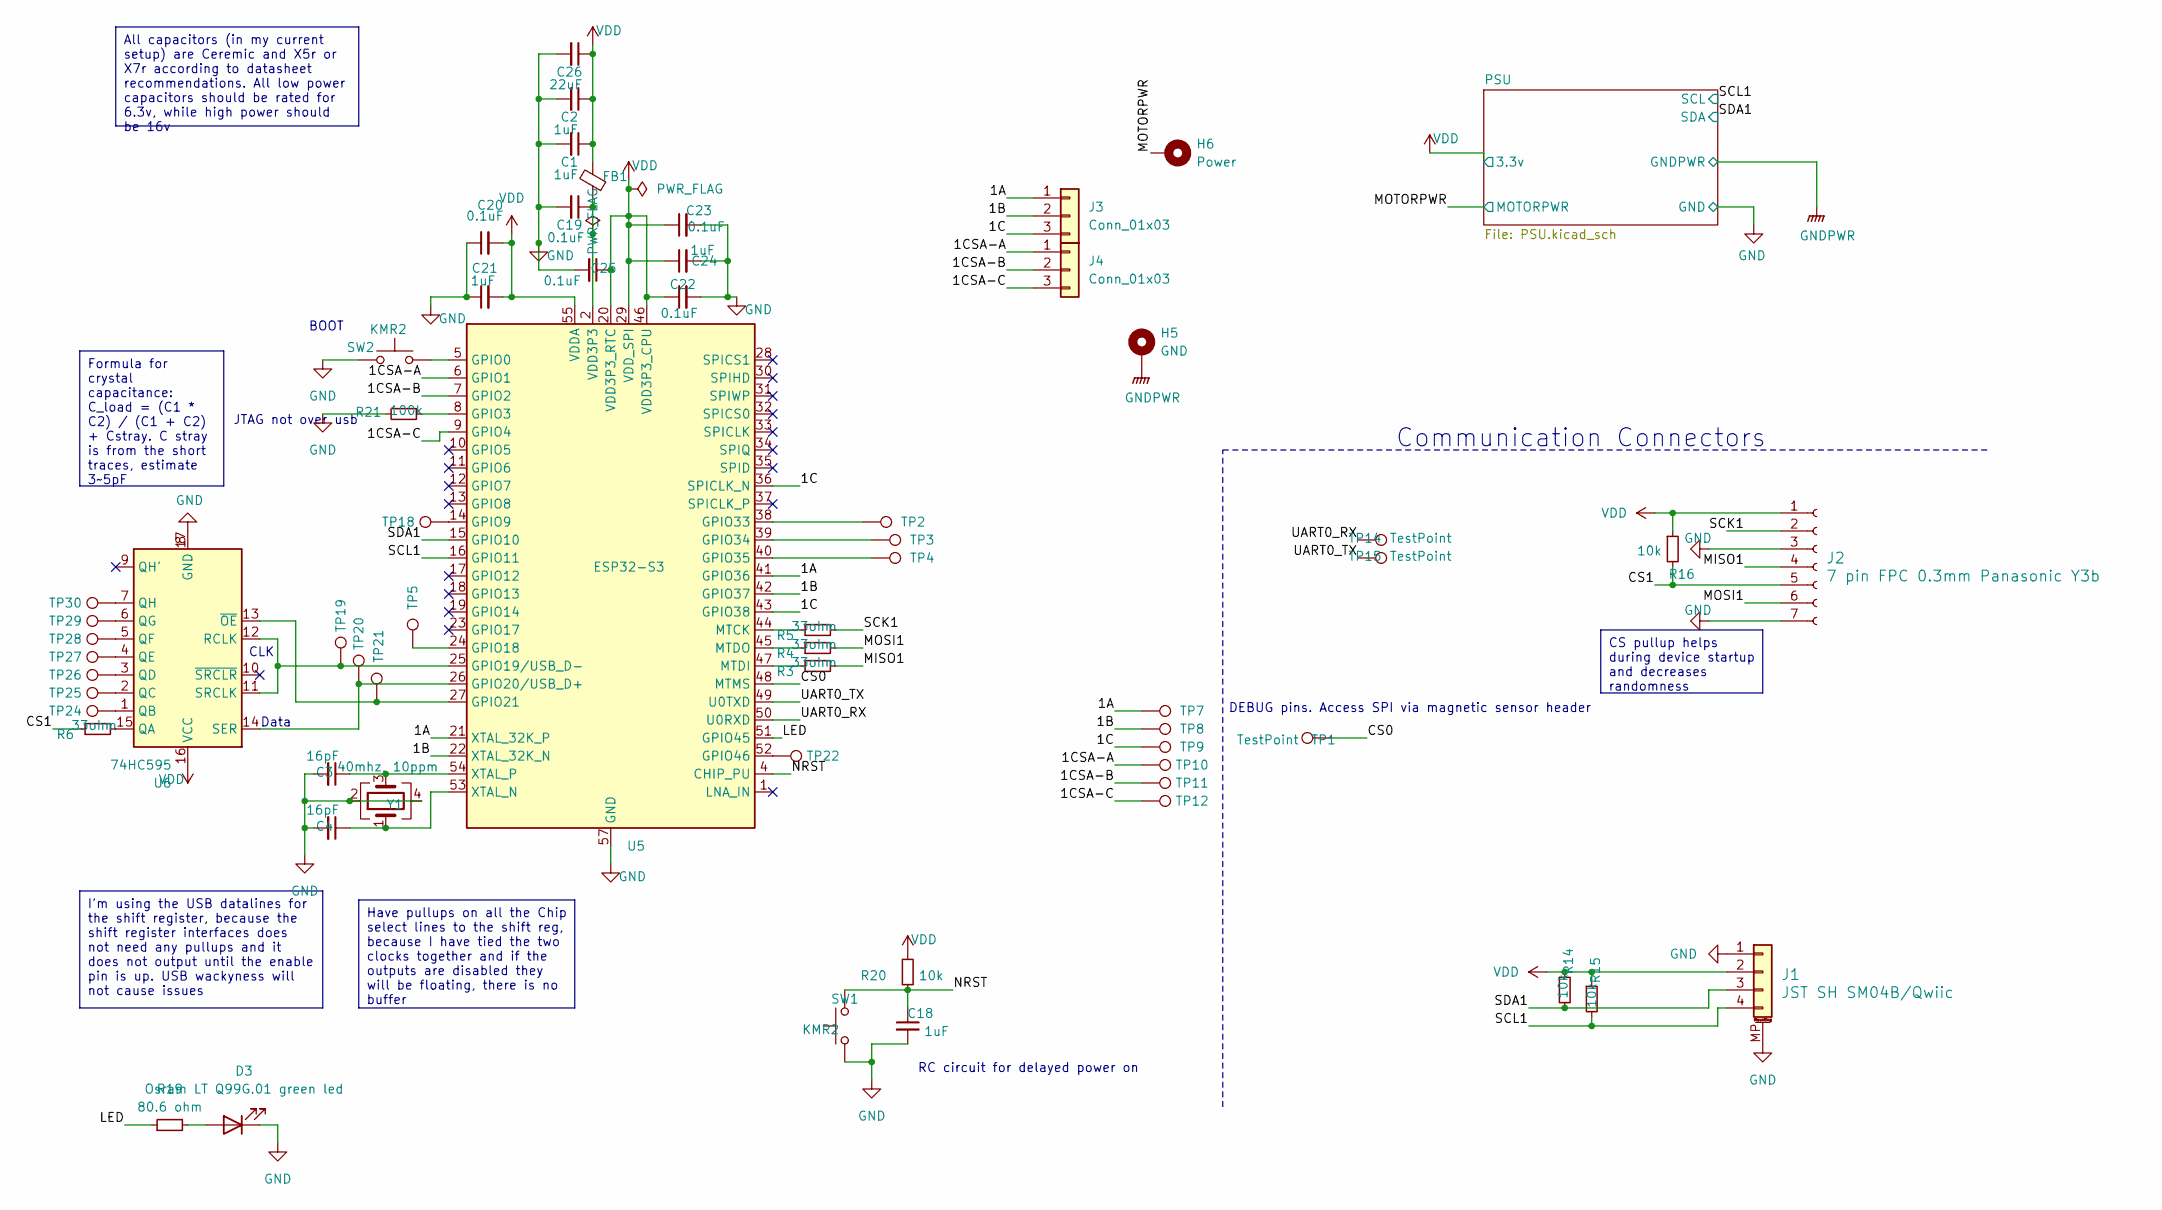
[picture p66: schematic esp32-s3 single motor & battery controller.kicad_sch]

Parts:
C1, C2, C21, C24: 1uF; C_0603_1608Metric
C3, C4: 16pF; C_0603_1608Metric_Pad1.08x0.95mm_HandSolder
C18: 1uF; C_0603_1608Metric_Pad1.08x0.95mm_HandSolder
C19, C20, C22, C23, C25: 0.1uF; C_0603_1608Metric
C26: 22uF; C_0603_1608Metric
D3: Osram LT Q99G.01 green led; LED_0603_1608Metric_Pad1.05x0.95mm_HandSolder
FB1: 120ohm imp @100mhz; L_0603_1608Metric
H5: GND; TestPoint_Pad_D2.0mm
H6: Power; TestPoint_Pad_D2.0mm
J1: JST SH SM04B/Qwiic; JST_SH_SM04B-SRSS-TB_1x04-1MP_P1.00mm_Horizontal
J2: 7 pin FPC 0.3mm Panasonic Y3b; fpc_7pin_0.3mm_connector Panasonic
J3, J4: Conn_01x03; PinHeader_1x03_P1.27mm_Vertical
R3, R4, R5, R6: 33ohm; R_0603_1608Metric
R14, R15, R16, R20: 10k; R_0603_1608Metric
R19: 80.6 ohm; R_0603_1608Metric
R21: 100k; R_0603_1608Metric
SW1, SW2: KMR2; SW_Push_1P1T_NO_CK_KMR2
TP1, TP14, TP15: TestPoint; TestPoint_Pad_D1.0mm
TP2, TP3, TP4, TP5, TP7, TP8, TP9, TP10, TP11, TP12, TP18, TP19, TP20, TP21, TP22, TP24, TP25, TP26, TP27, TP28, TP29, TP30: TestPoint_Pad_D1.0mm
U5: ESP32-S3; QFN-56-1EP_7x7mm_P0.4mm_EP4x4mm
U6: 74HC595; DHVQFN-16-1EP_2.5x3.5mm_P0.5mm_EP1x2mm
Y1: 40mhz, 10ppm; Crystal_SMD_3225-4Pin_3.2x2.5mm

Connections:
/1A: J3.1, TP7.1, U5.21 (XTAL_32K_P), U5.41 (GPIO36)
/1B: J3.2, TP8.1, U5.22 (XTAL_32K_N), U5.42 (GPIO37)
/1C: J3.3, TP9.1, U5.36 (SPICLK_N), U5.43 (GPIO38)
/1CSA-A: J4.1, TP10.1, U5.6 (GPIO1)
/1CSA-B: J4.2, TP11.1, U5.7 (GPIO2)
/1CSA-C: J4.3, TP12.1, U5.9 (GPIO4)
/CS0: TP1.1, U5.48 (MTMS)
/CS1: J2.5, R6.1, R16.2
/LED: R19.1, U5.51 (GPIO45)
/MISO1: J2.4, R3.2
/MOSI1: J2.6, R4.2
/MOTORPWR: H6.1; also elsewhere on the board
/NRST: C18.1, R20.1, SW1.2, U5.4 (CHIP_PU)
/SCK1: J2.2, R5.2
/SCL1: J1.4, R15.2, U5.16 (GPIO11); also elsewhere on the board
/SDA1: J1.3, R14.2, U5.15 (GPIO10); also elsewhere on the board
/UART0_RX: TP14.1, U5.50 (U0RXD)
/UART0_TX: TP15.1, U5.49 (U0TXD)
GND: C1.2, C2.2, C3.2, C4.2, C18.2, C19.2, C20.1, C21.1, C22.2, C23.2, C24.2, C25.2, C26.2, D3.1 (K), J1.1, J1.MP (MountPin), J2.3, J2.7, R21.2, SW1.1, SW2.1, U5.57 (GND), U6.8 (GND), U6.17 (GND), Y1.2, Y1.4; also elsewhere on the board
GNDPWR: H5.1; also elsewhere on the board
unnamed: C19.1, FB1.1, U5.2 (VDD3P3), U5.3 (VDD3P3)
unnamed: D3.2 (A), R19.2
unnamed: SW2.2, U5.5 (GPIO0)
unnamed: R21.1, U5.8 (GPIO3)
unnamed: TP18.1, U5.14 (GPIO9)
unnamed: TP5.1, U5.24 (GPIO18)
unnamed: TP19.1, U5.25 (GPIO19/USB_D-), U6.11 (SRCLK), U6.12 (RCLK)
unnamed: TP20.1, U5.26 (GPIO20/USB_D+), U6.14 (SER)
unnamed: TP21.1, U5.27 (GPIO21), U6.13 (~OE)
unnamed: TP2.1, U5.38 (GPIO33)
unnamed: TP3.1, U5.39 (GPIO34)
unnamed: TP4.1, U5.40 (GPIO35)
unnamed: TP22.1, U5.52 (GPIO46)
unnamed: R5.1, U5.44 (MTCK)
unnamed: R3.1, U5.47 (MTDI)
unnamed: R4.1, U5.45 (MTDO)
unnamed: C4.1, U5.53 (XTAL_N), Y1.1
unnamed: C3.1, U5.54 (XTAL_P), Y1.3
unnamed: R6.2, U6.15 (QA)
unnamed: TP24.1, U6.1 (QB)
unnamed: TP25.1, U6.2 (QC)
unnamed: TP26.1, U6.3 (QD)
unnamed: TP27.1, U6.4 (QE)
unnamed: TP28.1, U6.5 (QF)
unnamed: TP29.1, U6.6 (QG)
unnamed: TP30.1, U6.7 (QH)
VDD: C1.1, C2.1, C20.2, C21.2, C22.1, C23.1, C24.1, C25.1, C26.1, FB1.2, J1.2, J2.1, R14.1, R15.1, R16.1, R20.2, U5.20 (VDD3P3_RTC), U5.29 (VDD_SPI), U5.46 (VDD3P3_CPU), U5.55 (VDDA), U5.56 (VDDA), U6.16 (VCC); also elsewhere on the board

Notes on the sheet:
CS pullup helps during device startup and decreases randomness
All capacitors (in my current setup) are Ceremic and X5r or X7r according to datasheet recommendations. All low power capacitors should be rated for 6.3v, while high power should be 16v
Formula for crystal capacitance: C_load = (C1 * C2) / (C1 + C2) + Cstray. C stray is from the short traces, estimate 3~5pF
Have pullups on all the Chip select lines to the shift reg, because I have tied the two clocks together and if the outputs are disabled they will be floating, there is no buffer
I'm using the USB datalines for the shift register, because the shift register interfaces does not need any pullups and it does not output until the enable pin is up. USB wackyness will not cause issues
Communication Connectors
JTAG not over usb
RC circuit for delayed power on
Data
BOOT
CLK
DEBUG pins. Access SPI via magnetic sensor header

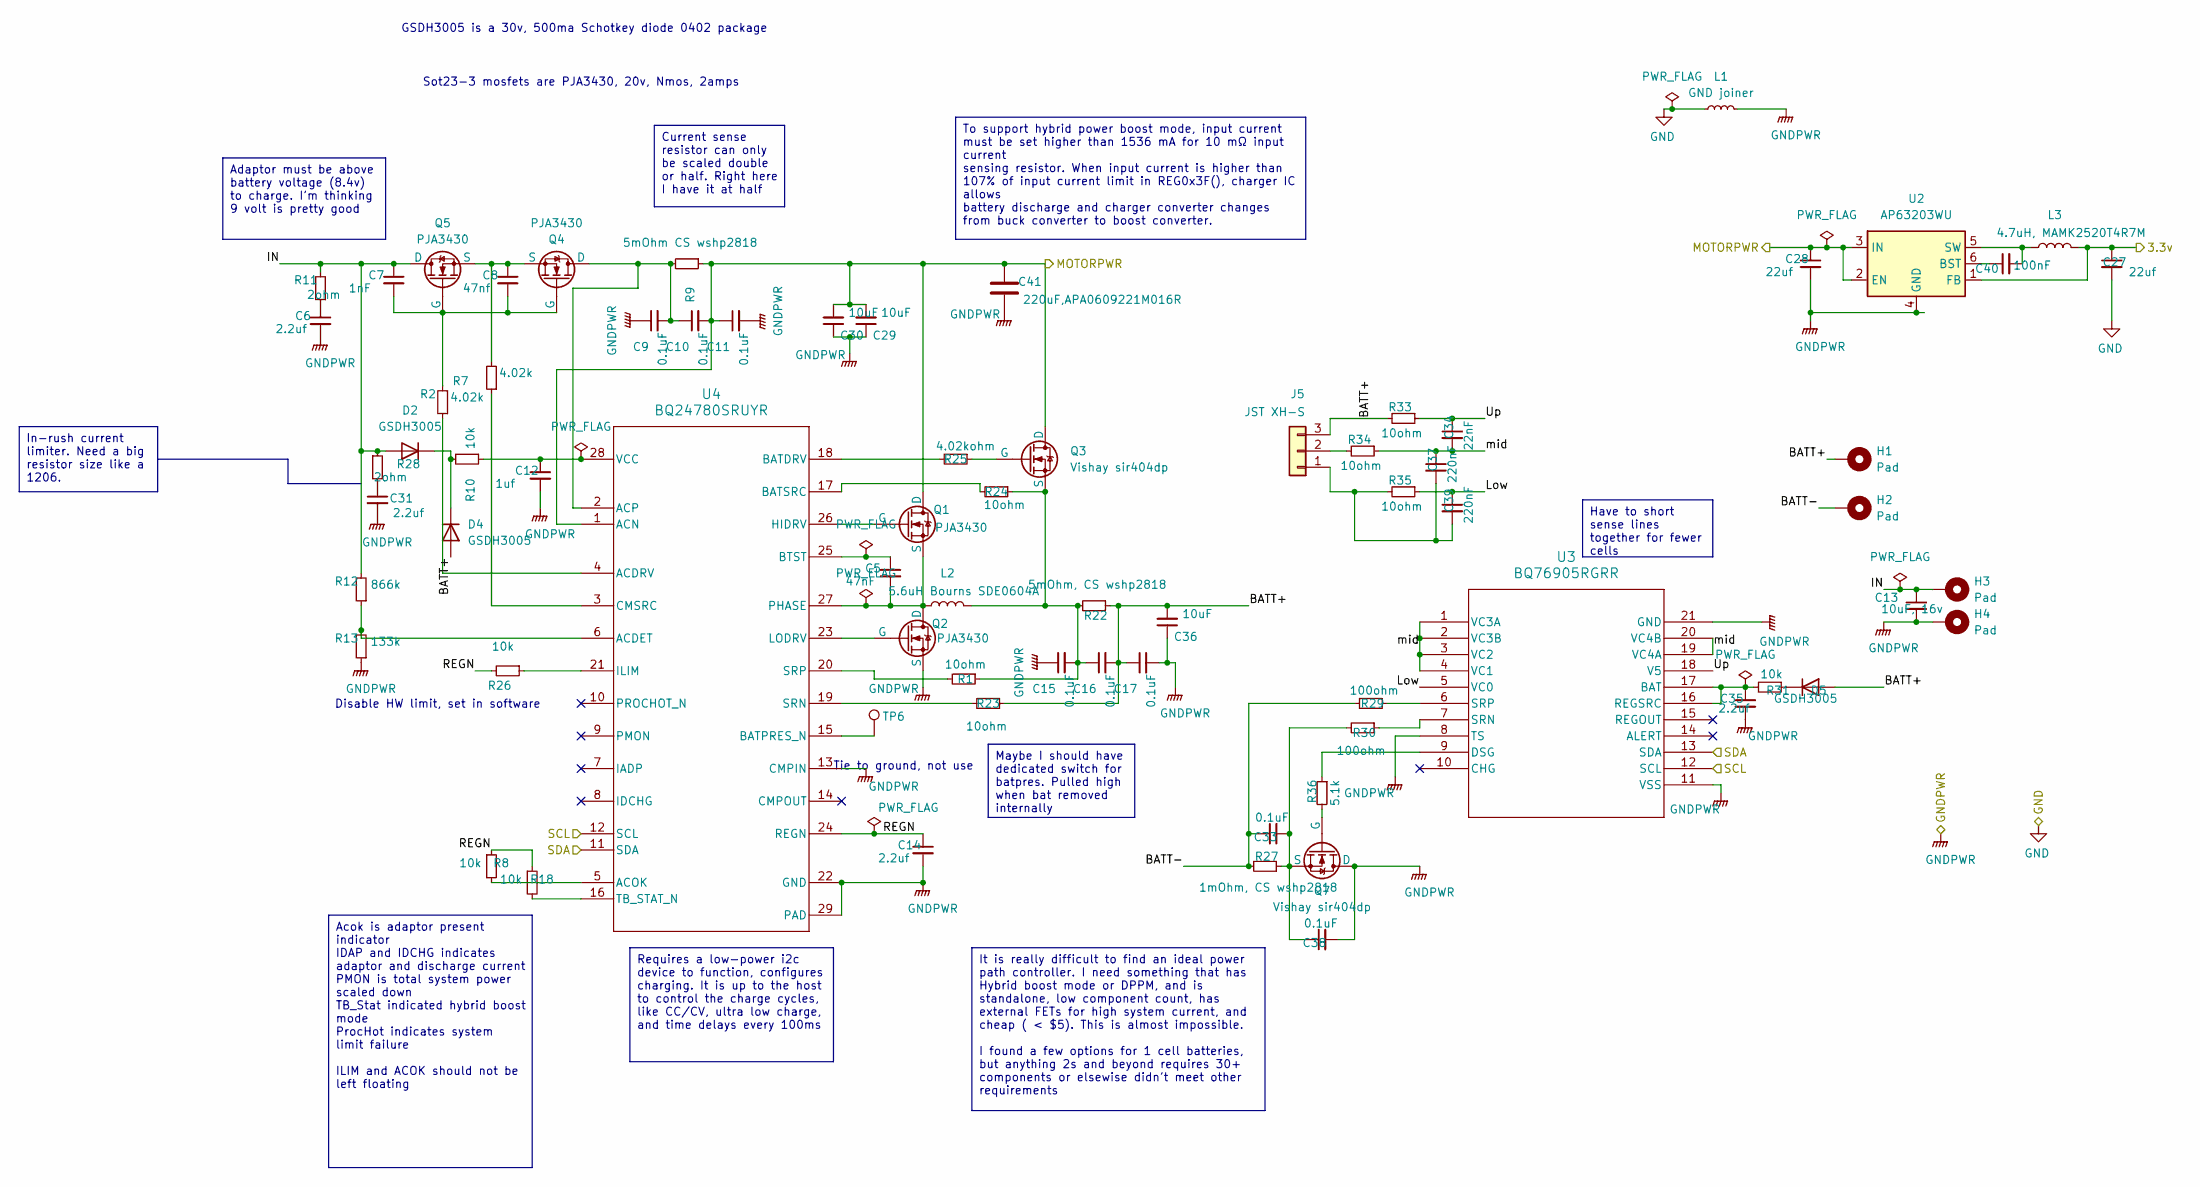
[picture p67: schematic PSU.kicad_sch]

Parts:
C5: 47nF; C_0603_1608Metric
C6, C14, C31, C35: 2.2uf; C_0603_1608Metric
C7: 1nF; C_0603_1608Metric
C8: 47nf; C_0603_1608Metric
C9, C10, C11, C15, C16, C17, C33, C38: 0.1uF; C_0603_1608Metric
C12: 1uf; C_0603_1608Metric
C13: 10uF, 16v; C_0603_1608Metric_Pad1.08x0.95mm_HandSolder
C27, C28: 22uf; C_0603_1608Metric
C29, C30, C36: 10uF; C_0603_1608Metric
C34: 22nF; C_0603_1608Metric
C37, C39: 220nF; C_0603_1608Metric
C40: 100nF; C_0603_1608Metric
C41: 220uF,APA0609221M016R; CP_Elec_6.3x9.9
D2, D4, D5: GSDH3005; D_0402_1005Metric
H1, H2, H3, H4: Pad; TestPoint_Pad_3.0x3.0mm
J5: JST XH-S; JST_XH_S3B-XH-A_1x03_P2.50mm_Horizontal
L1: GND joiner; SolderJumper-2_P1.3mm_Bridged_Pad1.0x1.5mm
L2: 5.6uH Bourns SDE0604A; L_Bourns_SDR0604
L3: 4.7uH, MAMK2520T4R7M; L_1008_2520Metric
Q1, Q2, Q4, Q5: PJA3430; SOT-323_SC-70
Q3, Q7: Vishay sir404dp; PQFN-8-EP_6x5mm_P1.27mm_Generic
R1, R23, R24, R33, R34, R35: 10ohm; R_0603_1608Metric
R2, R7: 4.02k; R_0603_1608Metric
R8, R10, R18, R26, R31: 10k; R_0603_1608Metric
R9: 5mOhm CS wshp2818; R_2816_7142Metric
R11, R28: 2ohm; R_0603_1608Metric
R12: 866k; R_0603_1608Metric
R13: 133k; R_0603_1608Metric
R22: 5mOhm, CS wshp2818; R_2816_7142Metric
R25: 4.02kohm; R_0603_1608Metric
R27: 1mOhm, CS wshp2818; R_2816_7142Metric
R29, R30: 100ohm; R_0603_1608Metric
R36: 5.1k; R_0603_1608Metric
TP6: TestPoint_Pad_D1.0mm
U2: AP63203WU; TSOT-23-6
U3: BQ76905RGRR; VQFN20_RGR_TEX
U4: BQ24780SRUYR; RUY0028A

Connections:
/MOTORPWR: C10.2, C11.1, C28.1, C29.2, C30.2, C41.1, Q1.1 (D), Q3.1 (D), Q3.2 (D), Q3.3 (D), R9.1, U2.2 (EN), U2.3 (IN), U4.1 (ACN); also elsewhere on the board
/PSU/BATT+: C16.2, C17.1, C36.2, D4.2 (A), D5.2 (A), H1.1, J5.3, R22.1, R23.1, R33.2
/PSU/BATT-: C33.1, H2.1, R27.2, R29.2
/PSU/IN: C7.1, C13.1, D2.2 (A), H3.1, Q5.1 (D), R11.2, R12.2, R28.1
/PSU/Low: C39.1, R35.1, U3.5 (VC0)
/PSU/REGN: C14.1, R8.1, R18.1, R26.2, U4.24 (REGN)
/PSU/Up: C34.1, R33.1, U3.18 (V5)
/PSU/mid: C34.2, C37.1, R34.1, U3.1 (VC3A), U3.2 (VC3B), U3.3 (VC2), U3.4 (VC1), U3.19 (VC4A), U3.20 (VC4B)
/SCL1: U3.12 (SCL), U4.12 (SCL); also elsewhere on the board
/SDA1: U3.13 (SDA), U4.11 (SDA); also elsewhere on the board
GND: C27.2, L1.1; also elsewhere on the board
GNDPWR: C6.2, C9.1, C11.2, C12.2, C13.2, C14.2, C15.1, C17.2, C28.2, C29.1, C30.1, C31.2, C35.2, C36.1, C38.2, C41.2, H4.1, L1.2, Q2.3 (S), Q7.1 (D), Q7.2 (D), Q7.3 (D), R13.1, U2.4 (GND), U3.8 (TS), U3.11 (VSS), U3.21 (GND), U4.13 (CMPIN), U4.22 (GND), U4.29 (PAD); also elsewhere on the board
unnamed: C6.1, R11.1
unnamed: C31.1, R28.2
unnamed: D2.1 (K), D4.1 (K), R10.2
unnamed: D5.1 (K), R31.1
unnamed: C37.2, C39.2, J5.1, R35.2
unnamed: J5.2, R34.2
unnamed: Q1.2 (G), U4.26 (HIDRV)
unnamed: C5.2, L2.1, Q1.3 (S), Q2.1 (D), U4.27 (PHASE)
unnamed: Q2.2 (G), U4.23 (LODRV)
unnamed: Q3.4 (G), R25.1
unnamed: C15.2, C16.1, L2.2, Q3.5 (S), R1.1, R22.2, R24.1
unnamed: C9.2, C10.1, Q4.1 (D), R9.2, U4.2 (ACP)
unnamed: C7.2, C8.2, Q4.2 (G), Q5.2 (G), R2.2
unnamed: C8.1, Q4.3 (S), Q5.3 (S), R7.2
unnamed: Q7.4 (G), R36.2
unnamed: C33.2, C38.1, Q7.5 (S), R27.1, R30.2
unnamed: C40.1, U2.6 (BST)
unnamed: C40.2, L3.1, U2.5 (SW)
unnamed: C35.1, R31.2, U3.16 (REGSRC), U3.17 (BAT)
unnamed: R36.1, U3.9 (DSG)
unnamed: R30.1, U3.7 (SRN)
unnamed: R29.1, U3.6 (SRP)
unnamed: R12.1, R13.2, U4.6 (ACDET)
unnamed: R2.1, U4.4 (ACDRV)
unnamed: R8.2, U4.5 (ACOK)
unnamed: R25.2, U4.18 (BATDRV)
unnamed: TP6.1, U4.15 (BATPRES_N)
unnamed: R24.2, U4.17 (BATSRC)
unnamed: C5.1, U4.25 (BTST)
unnamed: R7.1, U4.3 (CMSRC)
unnamed: R26.1, U4.21 (ILIM)
unnamed: R23.2, U4.19 (SRN)
unnamed: R1.2, U4.20 (SRP)
unnamed: R18.2, U4.16 (TB_STAT_N)
unnamed: C12.1, R10.1, U4.28 (VCC)
VDD: C27.1, L3.2, U2.1 (FB); also elsewhere on the board

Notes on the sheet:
It is really difficult to find an ideal power path controller. I need something that has Hybrid boost mode or DPPM, and is standalone, low component count, has external FETs for high system current, and cheap ( < $5). This is almost impossible. I found a few options for 1 cell batteries, but anythi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
Adaptor must be above battery voltage (8.4v) to charge. I'm thinking 9 volt is pretty good
Maybe I should have dedicated switch for batpres. Pulled high when bat removed internally
In-rush current limiter. Need a big resistor size like a 1206.
Requires a low-power i2c device to function, configures charging. It is up to the host to control the charge cycles, like CC/CV, ultra low charge, and time delays every 100ms
Current sense resistor can only be scaled double or half. Right here I have it at half
To support hybrid power boost mode, input current must be set higher than 1536 mA for 10 mΩ input current sensing resistor. When input current is higher than 107% of input current limit in REG0x3F(), charger IC allows battery discharge and charger converter changes from buck converter to boost conv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
Have to short sense lines together for fewer cells
Acok is adaptor present indicator IDAP and IDCHG indicates adaptor and discharge current PMON is total system power scaled down TB_Stat indicated hybrid boost mode ProcHot indicates system limit failure ILIM and ACOK should not be left floating
Sot23-3 mosfets are PJA3430, 20v, Nmos, 2amps
Tie to ground, not use
Disable HW limit, set in software
GSDH3005 is a 30v, 500ma Schotkey diode 0402 package

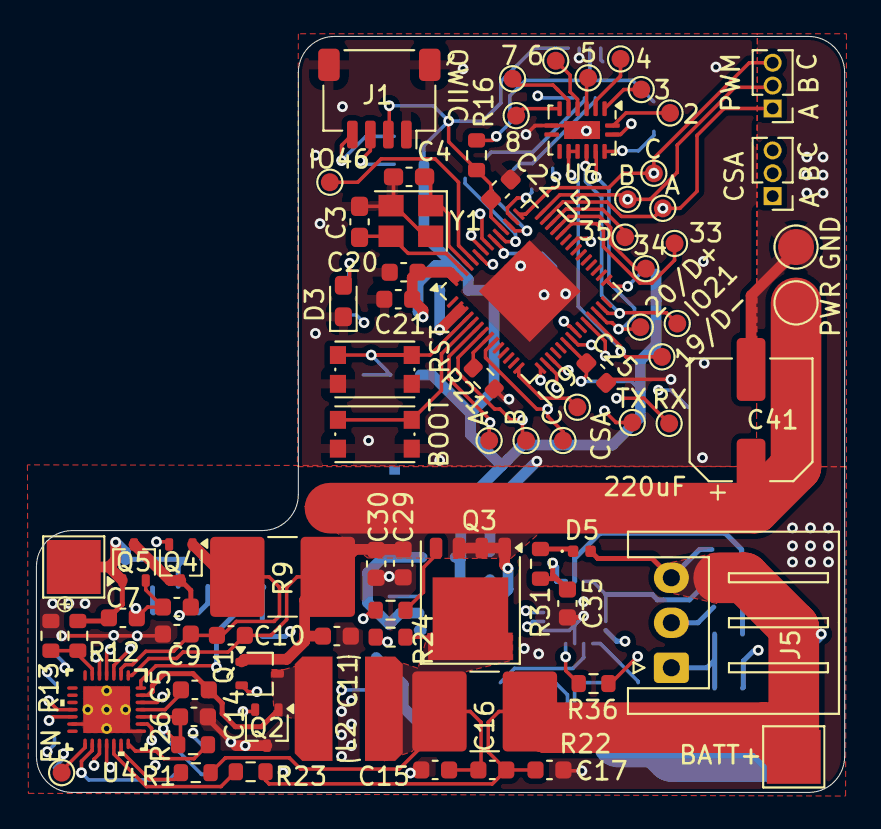
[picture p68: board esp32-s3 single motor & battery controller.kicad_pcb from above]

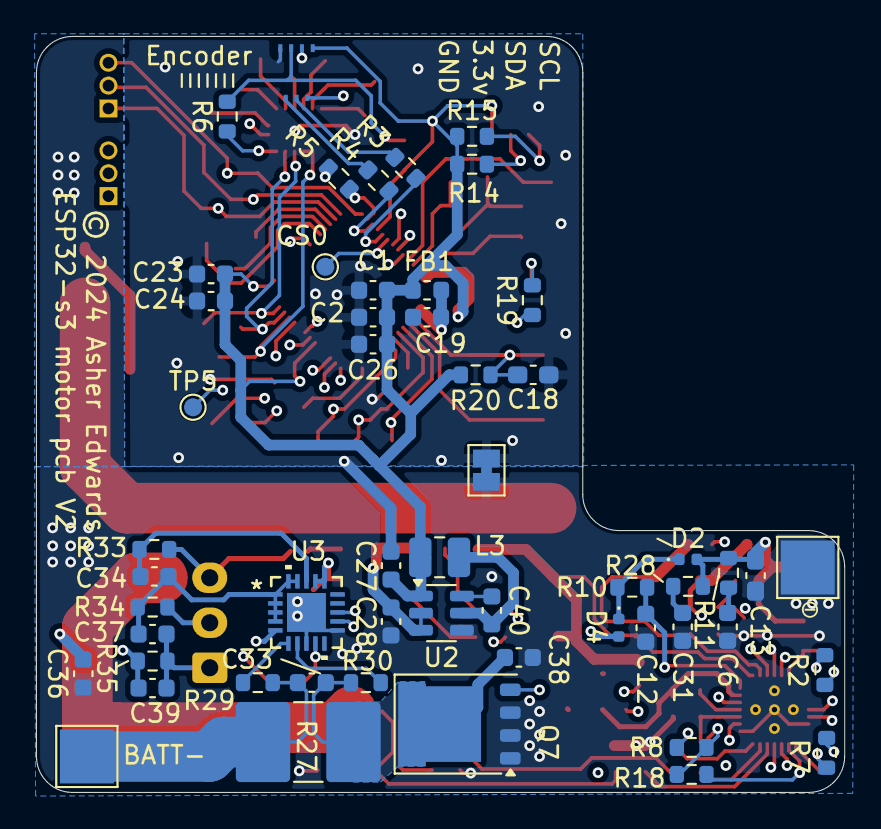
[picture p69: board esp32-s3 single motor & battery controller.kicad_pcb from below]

Board: 4 copper layers, 44.9 x 42.0 mm, 133 parts (54 on the bottom side), 89 nets.

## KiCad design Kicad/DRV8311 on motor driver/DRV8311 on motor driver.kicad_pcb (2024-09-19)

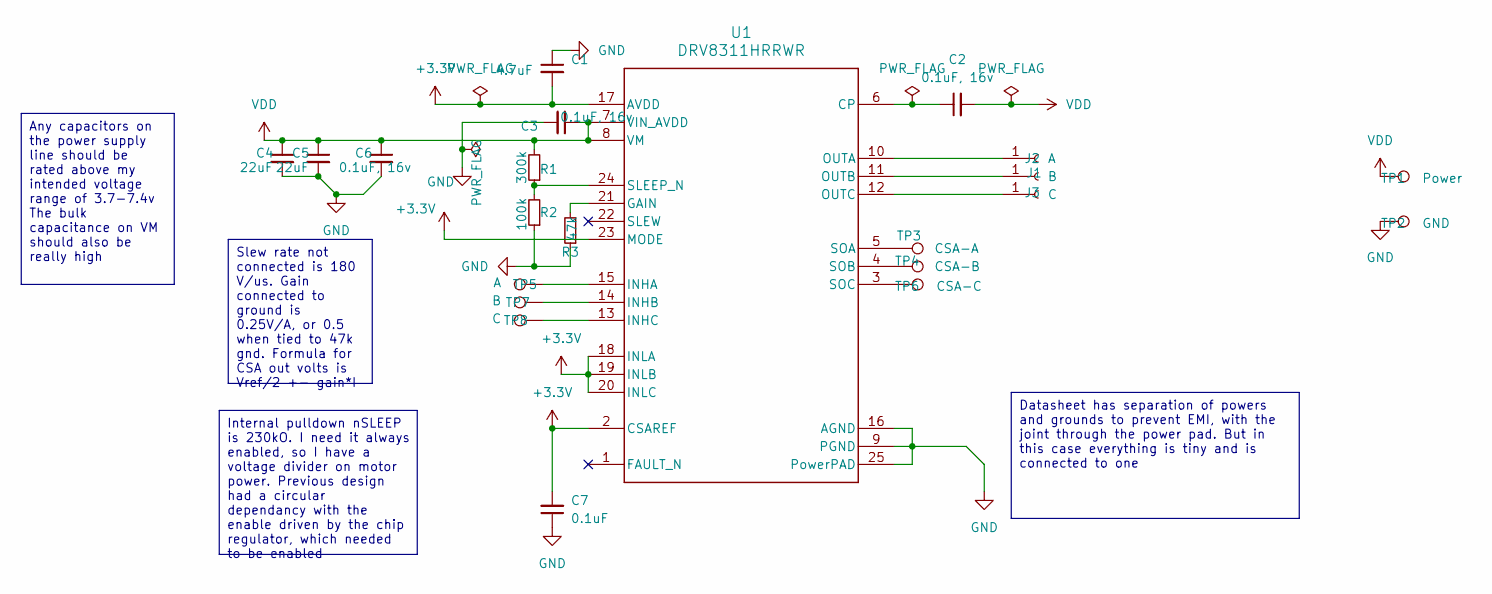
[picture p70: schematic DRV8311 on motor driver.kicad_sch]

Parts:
C1: 4.7uF; C_0402_1005Metric
C2, C3, C6: 0.1uF, 16v; C_0402_1005Metric
C4, C5: 22uF; C_0402_1005Metric
C7: 0.1uF; C_0402_1005Metric
J1: B; PinHeader_1x01_P1.27mm_Round
J2: A; PinHeader_1x01_P1.27mm_Round
J3: C; PinHeader_1x01_P1.27mm_Round
R1: 300k; R_0402_1005Metric
R2: 100k; R_0402_1005Metric
R3: 47k; R_0402_1005Metric
TP1: Power; TestPoint_Pad_D2.0mm
TP2: GND; TestPoint_Pad_D2.0mm
TP3: CSA-A; TestPoint_Pad_D1.0mm
TP4: CSA-B; TestPoint_Pad_D1.0mm
TP5: A; TestPoint_Pad_D1.0mm
TP6: CSA-C; TestPoint_Pad_D1.0mm
TP7: B; TestPoint_Pad_D1.0mm
TP8: C; TestPoint_Pad_D1.0mm
U1: DRV8311HRRWR; DRV8311_0.3mmVias

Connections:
+3.3V: C1.2, C7.2, U1.2 (CSAREF), U1.17 (AVDD), U1.18 (INLA), U1.19 (INLB), U1.20 (INLC), U1.23 (MODE)
GND: C1.1, C3.2, C4.2, C5.2, C6.2, C7.1, R2.1, R3.1, TP2.1, U1.9 (PGND), U1.16 (AGND), U1.25 (PowerPAD)
unnamed: J1.1, U1.11 (OUTB)
unnamed: J2.1, U1.10 (OUTA)
unnamed: J3.1, U1.12 (OUTC)
unnamed: C2.1, U1.6 (CP)
unnamed: R3.2, U1.21 (GAIN)
unnamed: TP5.1, U1.15 (INHA)
unnamed: TP7.1, U1.14 (INHB)
unnamed: TP8.1, U1.13 (INHC)
unnamed: R1.1, R2.2, U1.24 (SLEEP_N)
unnamed: TP3.1, U1.5 (SOA)
unnamed: TP4.1, U1.4 (SOB)
unnamed: TP6.1, U1.3 (SOC)
VDD: C2.2, C3.1, C4.1, C5.1, C6.1, R1.2, TP1.1, U1.7 (VIN_AVDD), U1.8 (VM)

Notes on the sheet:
Internal pulldown nSLEEP is 230kO. I need it always enabled, so I have a voltage divider on motor power. Previous design had a circular dependancy with the enable driven by the chip regulator, which needed to be enabled
Slew rate not connected is 180 V/us. Gain connected to ground is 0.25V/A, or 0.5 when tied to 47k gnd. Formula for CSA out volts is Vref/2 +- gain*I
Datasheet has separation of powers and grounds to prevent EMI, with the joint through the power pad. But in this case everything is tiny and is connected to one
Any capacitors on the power supply line should be rated above my intended voltage range of 3.7-7.4v The bulk capacitance on VM should also be really high

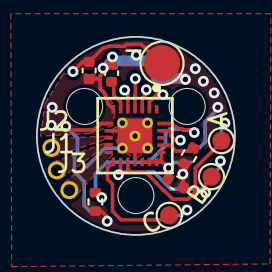
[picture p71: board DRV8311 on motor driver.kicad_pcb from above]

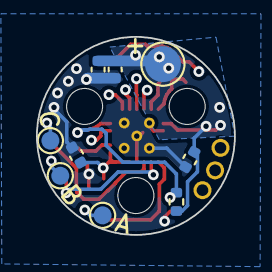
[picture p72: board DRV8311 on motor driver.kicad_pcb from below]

Board: 4 copper layers, 11.0 x 11.0 mm, 22 parts (9 on the bottom side), 15 nets.

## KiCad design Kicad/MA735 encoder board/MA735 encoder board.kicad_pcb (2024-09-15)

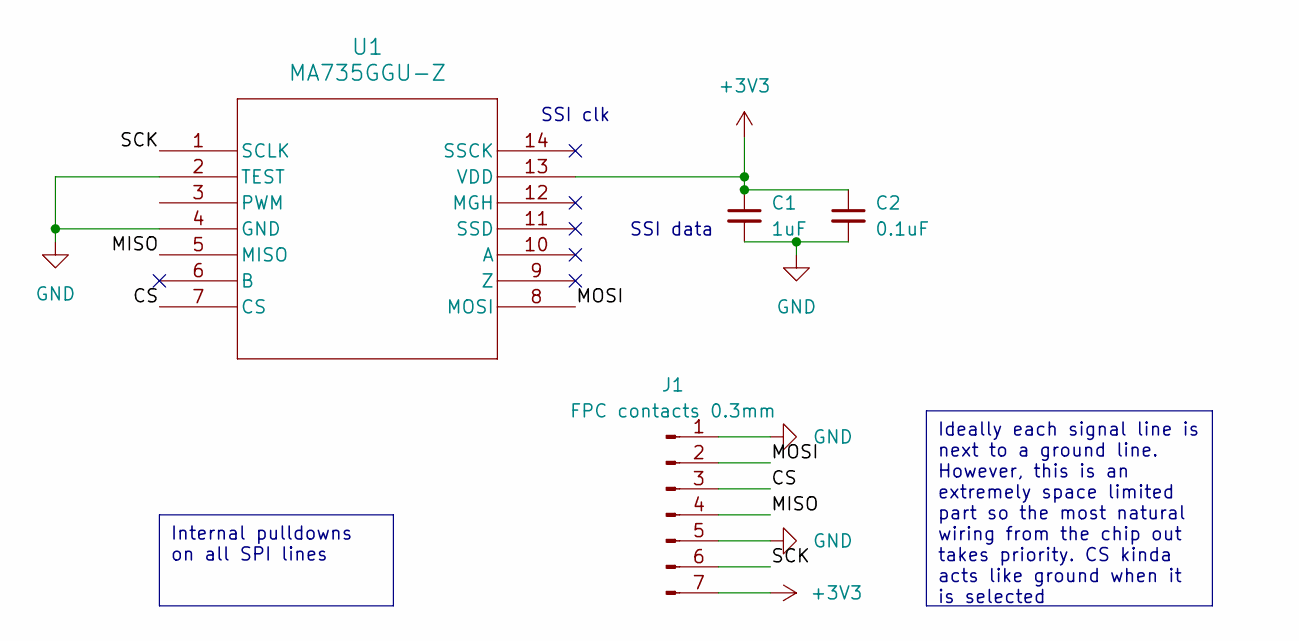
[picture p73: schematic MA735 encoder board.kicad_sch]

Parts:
C1: 1uF; C_0402_1005Metric
C2: 0.1uF; C_0402_1005Metric
J1: FPC contacts 0.3mm; 7pin_fpc_contact_0.3mmptich
U1: MA735GGU-Z; UTQFN-14_MA735_MNP

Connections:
+3V3: C1.1, C2.1, J1.7, U1.13 (VDD)
/CS: J1.3, U1.7 (CS)
/MISO: J1.4, U1.5 (MISO)
/MOSI: J1.2, U1.8 (MOSI)
/SCK: J1.6, U1.1 (SCLK)
GND: C1.2, C2.2, J1.1, J1.5, U1.2 (TEST), U1.4 (GND)

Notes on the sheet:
Ideally each signal line is next to a ground line. However, this is an extremely space limited part so the most natural wiring from the chip out takes priority. CS kinda acts like ground when it is selected
Internal pulldowns on all SPI lines
SSI clk
SSI data

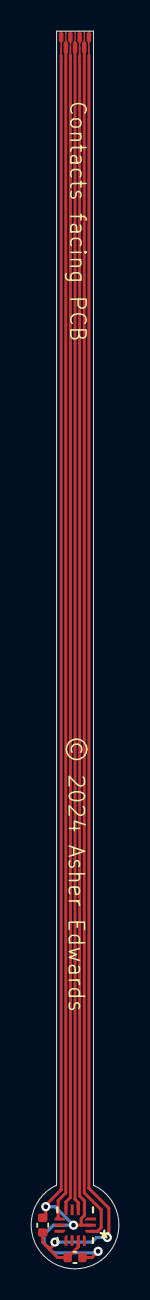
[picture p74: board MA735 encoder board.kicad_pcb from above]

Board: 2 copper layers, 5.7 x 80.4 mm, 4 parts (0 on the bottom side), 6 nets.

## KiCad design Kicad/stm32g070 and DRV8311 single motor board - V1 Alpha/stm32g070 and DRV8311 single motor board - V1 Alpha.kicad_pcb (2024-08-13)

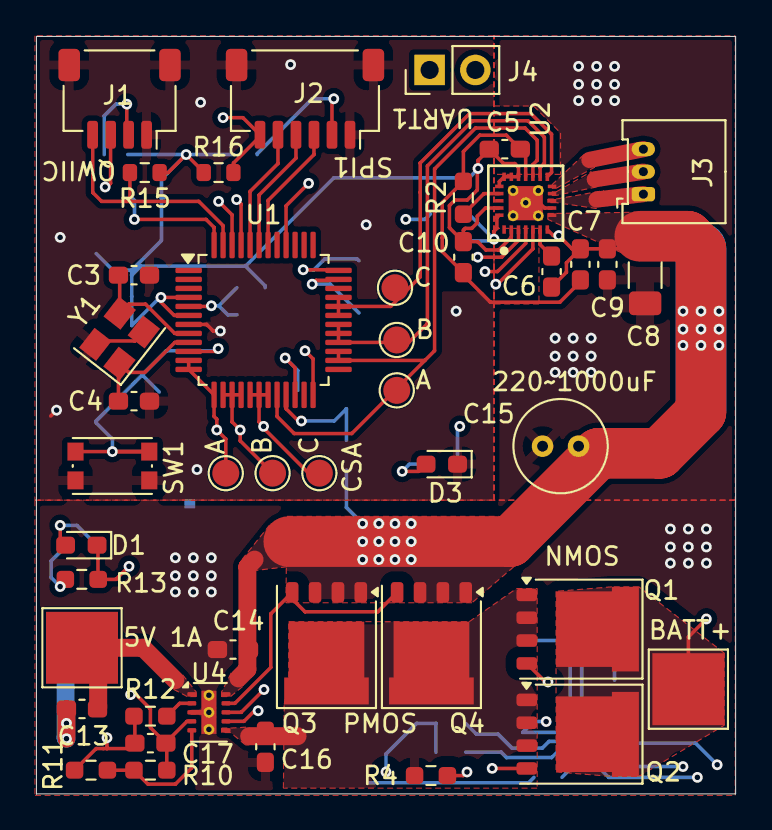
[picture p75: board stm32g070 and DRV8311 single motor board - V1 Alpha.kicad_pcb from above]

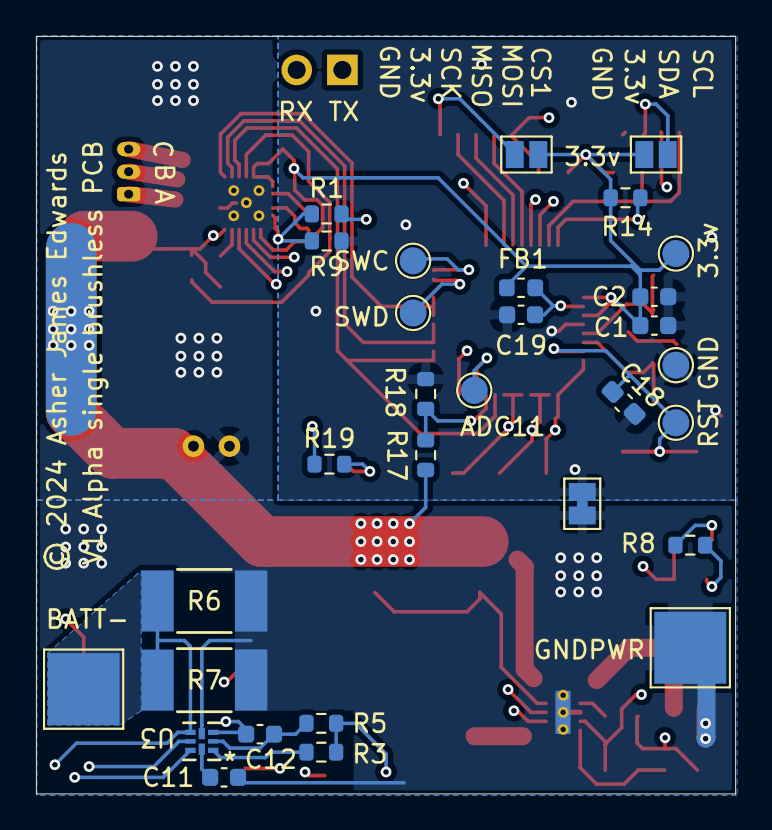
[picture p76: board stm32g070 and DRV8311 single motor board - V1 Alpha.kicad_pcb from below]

Board: 4 copper layers, 38.8 x 42.1 mm, 74 parts (30 on the bottom side), 51 nets.

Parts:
C1, C19: 0.1uF; C_0603_1608Metric
C2: 4.7uF; C_0603_1608Metric
C3, C4: 12pF; C_0603_1608Metric_Pad1.08x0.95mm_HandSolder
C5: 4.7uF; C_0603_1608Metric_Pad1.08x0.95mm_HandSolder
C6, C7, C9: 0.1uF, 16v; C_0603_1608Metric_Pad1.08x0.95mm_HandSolder
C8: 220uF, 16 v; C_1206_3216Metric_Pad1.33x1.80mm_HandSolder
C10, C18: 0.1uF; C_0603_1608Metric_Pad1.08x0.95mm_HandSolder
C11: 8nF; C_0603_1608Metric
C12: 1uF, 16v; C_0603_1608Metric
C13, C14, C16: 10uF, 16v; C_0603_1608Metric_Pad1.08x0.95mm_HandSolder
C15: 1000uF, 16v; C_Radial_D5.0mm_H5.0mm_P2.00mm
C17: 1uF; C_0603_1608Metric_Pad1.08x0.95mm_HandSolder
D1, D3: Osram LT Q99G.01 green led; LED_0603_1608Metric_Pad1.05x0.95mm_HandSolder
FB1: 120ohm imp @100mhz; L_0603_1608Metric
H1, H2, H3, H4: 4mm_Pad; TestPoint_Pad_4.0x4.0mm
J1: JST SH SM04B; JST_SH_SM04B-SRSS-TB_1x04-1MP_P1.00mm_Horizontal
J2: JST SH SM06B; JST_SH_SM06B-SRSS-TB_1x06-1MP_P1.00mm_Horizontal
J3: Molex_PicoBlade_53048-0310 Horizontal 3P; Molex_PicoBlade_53048-0310_1x03_P1.25mm_Horizontal
J4: Conn_01x02_Pin; PinHeader_1x02_P2.54mm_Vertical
JP1, JP2: VCC; SolderJumper-2_P1.3mm_Bridged_Pad1.0x1.5mm
L1: GND joiner; SolderJumper-2_P1.3mm_Bridged_Pad1.0x1.5mm
Q1: NMOS, sir404dp; PQFN-8-EP_6x5mm_P1.27mm_Generic
Q2: NMOS; PQFN-8-EP_6x5mm_P1.27mm_Generic
Q3: PMOS,Si7157DP; PQFN-8-EP_6x5mm_P1.27mm_Generic
Q4: PMOS; PQFN-8-EP_6x5mm_P1.27mm_Generic
R1, R17: 100k; R_0603_1608Metric
R2: 47k; R_0603_1608Metric_Pad0.98x0.95mm_HandSolder
R3: 20ohm; R_0603_1608Metric
R4, R13: 2k; R_0603_1608Metric_Pad0.98x0.95mm_HandSolder
R5: 300ohm; R_0603_1608Metric
R6: Same, 1000uOhm; RES_WSLF2512_VIS-M
R7: Vishay WSLF2512, 1%, 300uOhm; RES_WSLF2512_VIS-M
R8: 402 ohm; R_0603_1608Metric
R9, R18: 150k; R_0603_1608Metric
R10, R12: 1k; R_0603_1608Metric_Pad0.98x0.95mm_HandSolder
R11: 230ohm; R_0603_1608Metric_Pad0.98x0.95mm_HandSolder
R14, R15, R16: 10k; R_0603_1608Metric
R19: 80.6 ohm; R_0603_1608Metric
SW1: SW_Push; SW_Push_1P1T_NO_CK_KMR2
TP1, TP2, TP3, TP4, TP5, TP6: TestPoint; TestPoint_Pad_D1.5mm
TP7, TP8, TP9, TP10, TP11, TP12: TestPoint_Pad_D1.5mm
U1: STM32G070CBTr; LQFP-48_7x7mm_P0.5mm
U2: DRV8311HRRWR; DRV8311_0.3mmVias
U3: BQ298012RUGT; RUG8_TEX
U4: BQ25060; WSON-10-1EP_2x3mm_P0.5mm_EP0.84x2.4mm_ThermalVias_0.3mm
Y1: ABM8-16.000MHZ-10-1-U-T; Crystal_SMD_Abracon_ABM8G-4Pin_3.2x2.5mm

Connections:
/1A: TP7.1, U1.20 (PB1), U1.26 (PB14), U1.27 (PB15), U2.15 (INHA)
/1B: TP8.1, U1.28 (PA8), U1.29 (PA9/NC), U1.30 (PC6), U2.14 (INHB)
/1C: TP9.1, U1.31 (PC7), U1.32 (PA10/NC), U1.33 (PA11/PA9), U2.13 (INHC)
/1CSA-A: TP10.1, U1.11 (PA0), U1.12 (PA1), U1.13 (PA2), U2.5 (SOA)
/1CSA-B: TP11.1, U1.14 (PA3), U1.15 (PA4), U1.16 (PA5), U2.4 (SOB)
/1CSA-C: TP12.1, U1.17 (PA6), U1.18 (PA7), U1.19 (PB0), U2.3 (SOC)
/ADC10/VBATT: R17.1, R18.2, U1.21 (PB2)
/ADC11: TP6.1, U1.22 (PB10)
/CS1: J2.6, R16.2, U1.40 (PD2)
/LED: R19.1, U1.24 (PB12)
/MISO1: J2.4, U1.43 (PB4)
/MOSI1: J2.5, U1.44 (PB5)
/MOTORPWR: C6.2, C7.1, C8.1, C9.1, C14.1, C15.1, Q3.1 (S), Q3.2 (S), Q3.3 (S), Q4.1 (S), Q4.2 (S), Q4.3 (S), R1.2, R17.2, U2.7 (VIN_AVDD), U2.8 (VM), U4.10 (OUT)
/NRST: C18.1, SW1.2, TP1.1, U1.10 (NRST)
/PSU/BATT+: H1.1, Q1.5 (D), Q2.5 (D), R3.1, R5.1
/PSU/BATT-: C12.2, H2.1, R6.1, R7.1, U3.3 (VSS), U3.5 (CTR)
/PSU/IN: C13.1, H3.1, U4.1 (IN)
/PSU/LDO 4.9v: C17.2, R8.1, R10.1, R13.2, U4.4 (LDO)
/PSU/Pack+: C16.2, Q1.1 (S), Q1.2 (S), Q1.3 (S), Q2.1 (S), Q2.2 (S), Q2.3 (S), Q3.5 (D), Q4.5 (D), R4.1, U4.6 (BAT)
/PSU/~CHG: D1.1 (K), R13.1, U4.8 (~CHG)
/SCK1: J2.3, U1.42 (PB3)
/SCL1: J1.4, R15.2, U1.47 (PB8)
/SDA1: J1.3, R14.2, U1.48 (PB9)
/SWC: TP3.1, U1.36 (PA14)
/SWD: TP2.1, U1.35 (PA13)
/USART1_RX: J4.2, U1.46 (PB7)
/USART1_TX: J4.1, U1.45 (PB6)
GND: C1.2, C2.2, C3.2, C4.2, C5.1, C7.2, C10.1, C17.1, C18.2, C19.1, D3.1 (K), J1.1, J1.MP (MountPin), J2.1, J2.MP (MountPin), L1.1, R2.1, R9.1, R11.2, R12.1, R18.1, SW1.1, TP5.1, U1.7 (VSS), U2.16 (AGND), U4.7 (EN), Y1.2, Y1.4
GNDPWR: C8.2, C9.2, C11.2, C13.2, C14.2, C15.2, C16.1, H4.1, L1.2, R6.2, R7.2, U2.9 (PGND), U2.25 (PowerPAD), U3.4 (CS), U4.3 (VSS), U4.11 (VSS)
unnamed: D1.2 (A), R8.2
unnamed: D3.2 (A), R19.2
unnamed: J1.2, JP1.2 (B)
unnamed: J2.2, JP2.2 (B)
unnamed: J3.1, U2.10 (OUTA)
unnamed: J3.2, U2.11 (OUTB)
unnamed: J3.3, U2.12 (OUTC)
unnamed: Q1.4 (G), Q2.4 (G), U3.7 (DSG)
unnamed: Q3.4 (G), Q4.4 (G), U4.9 (BGATE)
unnamed: C3.1, U1.8 (PF0), Y1.3
unnamed: C4.1, U1.9 (PF1), Y1.1
unnamed: C19.2, FB1.1, U1.5 (VREF+)
unnamed: C6.1, U2.6 (CP)
unnamed: R2.2, U2.21 (GAIN)
unnamed: R1.1, R9.2, U2.24 (SLEEP_N)
unnamed: R3.2, U3.1 (BAT)
unnamed: C11.1, U3.8 (CHG)
unnamed: R4.2, U3.6 (PACK)
unnamed: C12.1, R5.2, U3.2 (VDD)
unnamed: R12.2, U4.2 (ISET)
unnamed: R10.2, R11.1, U4.5 (TS)
VDD: C1.1, C2.1, C5.2, C10.2, FB1.2, JP1.1 (A), JP2.1 (A), R14.1, R15.1, R16.1, TP4.1, U1.4 (VBAT), U1.6 (VDD), U2.2 (CSAREF), U2.17 (AVDD), U2.18 (INLA), U2.19 (INLB), U2.20 (INLC), U2.23 (MODE)

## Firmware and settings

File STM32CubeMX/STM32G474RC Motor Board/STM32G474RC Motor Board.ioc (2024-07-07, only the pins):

Mcu.UserName=STM32G474RCTx
PA0.Signal=ADC1_IN1
PA1.Signal=ADC1_IN2
PA10.Signal=S_TIM1_CH3
PA11.Signal=USB_DM
PA12.Signal=USB_DP
PA13.Signal=S_TIM4_CH3
PA14.Signal=I2C1_SDA
PA15.Signal=S_TIM8_CH1
PA2.Signal=ADC1_IN3
PA3.Signal=ADC1_IN4
PA4.Signal=ADC2_IN17
PA5.Signal=S_TIM2_CH1
PA6.Signal=ADC2_IN3
PA7.Signal=ADC2_IN4
PA8.Signal=S_TIM1_CH1
PA9.Signal=S_TIM1_CH2
PB0.Signal=ADC1_IN15
PB1.Signal=ADC1_IN12
PB10.Signal=S_TIM2_CH3
PB11.Signal=S_TIM2_CH4
PB12.Signal=ADC1_IN11
PB13.Signal=ADC3_IN5
PB14.Signal=ADC1_IN5
PB15.Signal=ADC2_IN15
PB2.Signal=S_TIM20_CH1
PB3.Signal=S_TIM2_CH2
PB4.Signal=S_TIM16_CH1
PB5.Signal=S_TIM17_CH1
PB6.Signal=S_TIM4_CH1
PB7.Signal=S_TIM3_CH4
PB8-BOOT0.Signal=I2C1_SCL
PB9.Signal=S_TIM4_CH4
PC0.Signal=ADC1_IN6
PC1.Signal=ADC1_IN7
PC10.Signal=SPI3_SCK
PC11.Signal=SPI3_MISO
PC12.Signal=SPI3_MOSI
PC2.Signal=S_TIM20_CH2
PC3.Signal=ADC1_IN9
PC4.Signal=ADC2_IN5
PC5.Signal=ADC2_IN11
PC6.Signal=S_TIM3_CH1
PC7.Signal=S_TIM3_CH2
PC8.Signal=S_TIM3_CH3
PC9.Signal=S_TIM8_CH4
PF0-OSC_IN.Signal=ADC1_IN10
PF1-OSC_OUT.Signal=ADC2_IN10

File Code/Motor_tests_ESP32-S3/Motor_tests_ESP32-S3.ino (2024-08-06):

#include "SPI.h"
#include "SimpleFOC.h"
#include "SimpleFOCDrivers.h"
#include "encoders/ma735/MagneticSensorMA735.h"
#include <Adafruit_NeoPixel.h>


//-----------------Pins-------------------

#define LED 21

#define CSA_A 1
#define CSA_B 2
#define CSA_C 3 

#define OUT_A 4  //GPIO 4
#define OUT_B 5  //GPIO 5
#define OUT_C 6  //GPIO 6

#define CS1 7  

unsigned long t0;
unsigned long t2;
int diff; //continuously calculated

//-------------------Interfaces-------------------------

SPIClass SPI_1(HSPI);// Had to move pin definitions to init

//                     num pixel, pin, pixel format
Adafruit_NeoPixel pixel(1, LED, NEO_GRB + NEO_KHZ800);

//-------------------Motor Driver--------------------

//  BLDCMotor( pole_pairs , ( phase_resistance, KV_rating  optional) )
BLDCMotor motor = BLDCMotor(6, 0.2, 22000);  //KV on my motor is 19000, docs suggest going 50% higher than that
//Pole pairs is the number of poles / 2. Phase resistance is 0.2 ohms, since I got 0.4 ohm between two leads and I saw a little wire tail indicating Wye configuration

// Update to the MA735 code after this
// MagneticSensorSPI(int cs, float bit_resolution, int angle_register)
//MagneticSensorSPI sensor = MagneticSensorSPI(CS1, 13, 0x3FFF);
MagneticSensorMA735 sensor(CS1);

//  BLDCDriver3PWM( pin_pwmA, pin_pwmB, pin_pwmC, enable (optional))
BLDCDriver3PWM driver = BLDCDriver3PWM(OUT_A, OUT_B, OUT_C);


//BROKEN IN 2.3.4. Something changed
//  LowsideCurrentSense(shunt_resistance, gain, adc_a, adc_b, adc_c)
LowsideCurrentSense current_sense = LowsideCurrentSense(0.01, 25, CSA_A, CSA_B, CSA_C);
//DRV8311 I set to have a gain of 0.25V/A. Translating this to resistance it should be 0.01ohms and 25 gain. V = IR, V = 1a*0.01. V is 0.01, x 25 = 0.25 volts an amp.

//instantiate commander
Commander command = Commander(Serial, '\n', false);

void onMotor(char* cmd) {
  command.motor(&motor, cmd);
}
void readSensor(char* cmd) {
  // get the angle, in radians, no full rotations
  float angle = sensor.getCurrentAngle();
  float degrees = angle * 360 / 6.28318530718;
  Serial.print("Angle (rad): ");
  Serial.println(angle, 7);  //7 specifies the decimal places
  Serial.print("Angle (deg): ");
  Serial.println(degrees, 5);

  // get the angle, in radians, including full rotations
  float angle_sum = sensor.getAngle();

  // get the velocity, in rad/s - note: you have to call getAngle() on a regular basis for it to work
  float vel = sensor.getVelocity();
  Serial.print("Velocity: ");
  Serial.println(vel);

  // get the field strength
  FieldStrength fs = sensor.getFieldStrength();
  Serial.print("Field strength: ");
  Serial.println(fs);
}

void flashLED(char* cmd) {
  pixel.setPixelColor(0, pixel.Color(100, 0, 0));
  pixel.show();
  delay(200);
  pixel.clear();
  pixel.show();
}

void readUpdateTime(char* cmd) {
  Serial.print("Update time");
  Serial.println(diff);
}


void setup() {
  pixel.begin();

  // use monitoring with the BLDCMotor
  Serial.begin(115200);
  while(!Serial && millis()<10000) {
    //wait for serial to connect, for up to 10 seconds
  }
  //Flash that serial is connected
  pixel.setPixelColor(0, pixel.Color(100, 0, 0));
  pixel.show();
  delay(200);
  pixel.clear();
  pixel.show();
  // monitoring port
  motor.useMonitoring(Serial);

  SimpleFOCDebug::enable(&Serial);  //enable debug code too

  // MA735 supports mode 0 and mode 3
  // In the driver I have it set to 20mhz instead of 1
  // initialize magnetic sensor hardware
  //     MOSI  MISO  SCLK  SSEL
  SPI_1.begin(8, 9, 10, CS1);
  sensor.init(&SPI_1);
  sensor.setResolution(9);
  // link the motor to the sensor
  motor.linkSensor(&sensor);

  //Note: Do not run register writes every time the program runs. The chip has only 1000 flash write cycles! My driver has a check for this, others do not!
  //sensor.setBiasCurrentTrimming(0);  //fine, since it is my driver

  //init driver
  // pwm frequency to be used [Hz]
  driver.pwm_frequency = 20000;
  // power supply voltage [V]
  driver.voltage_power_supply = 4.2;
  // driver init
  driver.init();
  // link the motor to the driver
  motor.linkDriver(&driver);

  // link the driver with the current sense
  current_sense.linkDriver(&driver);

  // Changing gain values to those in the drv8311 docs. I have to figure this out still. I may have to modifiy the library source to implement what the docs need
  //current_sense.gain_a = 1.0 / shunt_resistor / gain;
  //current_sense.gain_b = 1.0 / shunt_resistor / gain;
  //current_sense.gain_c = 1.0 / shunt_resistor / gain;

  // init current sense
  current_sense.init();
  current_sense.skip_align = true;//I am sure in my configuration
  // link the motor to current sense
  motor.linkCurrentSense(&current_sense);

  // set control loop type to be used
  motor.controller = MotionControlType::velocity;
  // voltage torque control mode
  motor.torque_controller = TorqueControlType::foc_current;//voltage, dc_current, or foc_current

  // choose FOC modulation
  // SinePWM; (default)
  // SpaceVectorPWM; Similar to sine wave, not sure the diff
  // Trapezoid_120; Faster,but less efficient
  // Trapezoid_150; Same, except the angle offset is more
  motor.foc_modulation = FOCModulationType::SpaceVectorPWM;//Trapezoid_120 is faster, but SVPWM is more efficient
  //motor.voltage_limit = 1;//Should be really low for drone motors. Ignored since I provided phase resistance
  motor.current_limit = 2.5;  // Amps

  motor.voltage_sensor_align = 0.5;//I=V/R. This should get me 2.5 current during alignment. I COMPLETELY spaced on this earlier when I set it to 5v and nothing happened (waveforms capped)
  //motor.zero_electric_angle = 1.65;//Skip alignment since I know the position. The auto align always gets alignment wrong and cause one direction to be faster than other.
  //motor.sensor_direction = Direction::CCW;


  // PID velocity
  motor.PID_velocity.P = 0.1;
  motor.PID_velocity.I = 4.0;
  motor.PID_velocity.D = 0.001;
  motor.PID_velocity.output_ramp = 1000;
  motor.LPF_velocity.Tf = 0.02;//seconds

  motor.PID_current_d.P = 0.2;
  motor.PID_current_d.I = 20.0;

  motor.PID_current_q.P = 0.2;
  motor.PID_current_q.I = 20.0;

  motor.motion_downsample = 2;

  // initialize motor
  motor.init();

  // align encoder and start FOC. This can be skipped once you have tuned your motor and got the absolute zero offset of the encoder. See docs
  motor.initFOC();
  //current_sense.driverAlign(1);

  command.add('M', onMotor, "my motor");  //default motor call;

  command.add('S', readSensor, "Read magnetic encoder");

  command.add('F', flashLED, "flashLED");
  command.add('T', readUpdateTime, "Read the update time");

  motor.monitor();

  //Finished setup so flash led
  pixel.setPixelColor(0, pixel.Color(100, 0, 0));
  pixel.show();
  delay(200);
  pixel.clear();
  pixel.show();
}

void loop() {
  t0=_micros();
  // FOC algorithm function
  motor.loopFOC();
  //driver.setPwm(1.1,2.5,4);

  // velocity control loop function
  // setting the target velocity to 2rad/s
  motor.move();

  if (motor.target == 0.0f && motor.enabled==1)
    motor.disable();
  if (motor.target != 0.0f && motor.enabled==0)
    motor.enable();

  // monitoring function outputting motor variables to the serial terminal
  motor.monitor();//This slows things down BTW!

  //PhaseCurrent_s currents = current_sense.getPhaseCurrents();
  //float current_magnitude = current_sense.getDCCurrent();

  // Serial.print(currents.a*1000); // milli Amps
  // Serial.print("\t");
  // Serial.print(currents.b*1000); // milli Amps
  // Serial.print("\t");
  // Serial.print(currents.c*1000); // milli Amps
  // Serial.print("\t");
  // Serial.println(current_magnitude*1000); // milli Amps

  // read user commands
  command.run();

  t2=_micros();
  diff = t2-t0;

}

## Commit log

2024-06-26 Adding current Kicad files
    I previously was not tracking these files on GitHub, so its a rather big commit.
    [DRV8311.kicad_sch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]
2024-07-04 Fixes to the PCB after production related to mosfets
    So..... I sourced the wrong mosfets. I chose mosfets with the marketing moniker PowerPAK, never thinking that could mean multiple footprint sizes. I sourced mosfets with the powerpak 1212 footprint, instead of the powerpak SO-8 footprint. They ended up being tiny and I had to do a bodge fix to test. I have replaced the mosfets in schematic with correctly sized ones now.
    Another change I made in this commit is related to LEDs. I sourced the leds and resistors last minute, so the values are a bit different than originally on the schematic. I realized too that my tri-state led status circuit wouldn't work, because the bq25060 status pin is n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
    [DRV8311.kicad_sch, PSU.kicad_sch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]
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2024-07-06 Fixing DRV8311 recursive design flaw, and pin tie issue
    Since I'm using 3x pwm mode for the driver, I should have tied the unused lowside pins to 3.3v, and not left them floating, according to the datasheet. This is fixed now
    The driver chip has an enable pin with an internal weak pulldown. I put a pull-up resistor on the outside, to always keep the chip on. Guess what that is connected to though? The regulator output from the chip, which is disabled! I fixed this in the design by have a voltage divider coming from motor power to enable the pin.
    [DRV8311.kicad_sch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]
2024-07-07 Updated progress log, Added Flipper zero programmer support
    Make sure to delete `.config/arduino-ide` to clear up the cache and get the programmer to show up.
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2024-07-07 Switched upload file type and extra parameters
    When uploading .bin files it would write to address 0x00000000 which is incorrect, it needs a boot offset. I switched to the .elf file, and the program uploaded a verified correctly. Also, specifying multiple extra parameters need to be on the same line.
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2024-07-08 Corrected CPU clock frequency
    It is now running at appropriate speed, and the uart baud rate is matching on both ends. 64mhz cpu Wohoo!
    [Blink.ino]
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2024-07-16 Fixed Analog read encoding error
    [System_tests.ino]
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2024-07-16 Current non-working SPI code
    I can't figure out what is wrong, but it breaks Serial for some reason
    [System_tests.ino]
2024-07-16 Working SPI sensor data read
    The issue was with the default pin definitions. I created an instance with the correct SPI pins.
    [System_tests.ino]
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2024-07-16 Working Magnetic sensor angle detection
    It seems like the field strength value is really only an indicator if it is the correct distance. It is a 1 when to far, 0 when just right, and 2 when too close. I think I have to modify the source driver code, because though the sensor models are similar (MA730, mine: MA735), they have slightly different registers.
    [Motor_tests.ino]
2024-07-17 Added missing registers and cmds
    The two that weren't already implemented was the resolution/speed tradeoff setting (Filter Window), and the ABZ hysteresis setting.
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2024-07-17 Fixed switch case typos
    It wasn't compiling last night, because of a few typos. Also switch statements only operate on integers or similar, not strings or floats.
    [Motor_tests.ino]
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2024-07-17 Update progress log, compiled code
    I had the wrong names for commander in some places. Code takes up 80kb!
    [Motor_tests.ino]
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2024-07-17 Fixed motor not doing anything
    I needed to call .move() in the main loop! I also need the pins to be on the same timer, because Simple foc couldn't find a master timer for any on Tim1. I guess tim1 should be reserved for master clock, everything else should be fine.
    [Motor_tests.ino]
2024-07-18 Some quick fixes
    The motors will spin, however it is only at 100 radians/s and it doesn't like other speeds higher or lower. It whines a lot.
    [Motor_tests.ino]
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2024-07-19 Fixed INL-C disconnect, alignment bug in code
    [Motor_tests.ino]
2024-07-19 Skip current sense alignment
    It worked on initialization, however it keeps swapping to the wrong pins. All the current sense align really does is checks and fixes pin errors, but I am pretty sure the pins match up
    [Motor_tests.ino]
2024-07-20 Finally Fixed motor sensor alignment issue
    I had forgotten about Ohms law in setting the voltage sensor alignment, which lead to a current beyond my systems capacity. The result was probably capped waveforms and the motor not moving. 25 amps of current if the voltage is set to 5 on my motor! I now set the the voltage sensor align to 0.5, which gives about 2.5 amps current during alignment.
    [Motor_tests.ino]
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2024-07-25 Start rework of gearbox base
    I am adding parametric variables in Onshape, and added screw holes that should universally support all my future gearboxes
    [base motor assembly - Motor.step, base motor assembly - bell.step, base motor assembly - motor mount.step]
2024-07-25 Updated dependent gearboxes, added fanblade
    I updated the magnetic sensor mount to be compatible with the new base design. I also added a little motor fan blade that probably won't work
    [base motor assembly - Motor.step, base motor assembly - bell.step, base motor assembly - center shaft.step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]
2024-07-25 Added fan blade on central shaft
    This is a paddle blade like found in power tools and drills. Its not a very efficient fan blade but it works in both directions. Onshape: https://cad.onshape.com/documents/c861ec30af8169cf9c14bd7f/w/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
    [base motor assembly - Motor.step, base motor assembly - bell.step, base motor assembly - center shaft.step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]
2024-07-25 Switching to multi-part STEP, partially fixed cycloidal
    The cycloidal gearbox I designed last month broke with the latest changes, and a lot has to be fixed. Onshape link: https://cad.onshape.com/documents/c861ec30af8169cf9c14bd7f/w/e538486c85e6a5fe77cd1d33/m/89253d69daa5255312b214bc/e/3c33a9dbb543ee5c67ba9708
    [Cycloidal No Bearings.step, base motor assembly - Motor.step, base motor assembly - bell.step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]
2024-07-26 Finished fixing the cycloidal main design
    The assembly is still broken though.
    Onshape: https://cad.onshape.com/documents/c861ec30af8169cf9c14bd7f/w/e538486c85e6a5fe77cd1d33/m/b9f96b10a7d62c04f2979a8a/e/3c33a9dbb543ee5c67ba9708
    [Cycloidal No Bearings.step]
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2024-07-26 Added bearing standoff
    I bought the wrong bearings, and spent a lot of time trying to think things out in my head. Ultimately there is no way I can fix it without buying bigger bearings
    Onshape https://cad.onshape.com/documents/c861ec30af8169cf9c14bd7f/w/e538486c85e6a5fe77cd1d33/m/1b6c93d1b7dc39d60db1a321/e/7383c3da91d908f3c2a75881
    [Cycloidal.step]
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2024-07-27 Started work on cutting down through hole axles
    It would be nice if I could just have 3 axles running through the cycloidal disc, plus whatever wires. I would need to remove the shafts and use the screws directly as center pins.
    This is complicated, and makes the disc 20mm in diameter. I want this to be small, so whatever is most space efficient is better. Bearings take up a lot of space of course, but low friction elements 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
    Onshape: https://cad.onshape.com/documents/c861ec30af8169cf9c14bd7f/w/e538486c85e6a5fe77cd1d33/m/c407a49b8466d73e4641e261/e/7383c3da91d908f3c2a75881
    [Cycloidal.step]
2024-07-27 Shrinking disc size
    Currently it looks like the smallest I can feasible go is 16mm. I have the number of teeth set to be divisible by 3, so the 3 axle bearings can nestle into the patter of the teeth. I also started wor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
    Onshape: https://cad.onshape.com/documents/c861ec30af8169cf9c14bd7f/w/e538486c85e6a5fe77cd1d33/m/ab9855c3639a3ccbf2450367/e/7383c3da91d908f3c2a75881
    [Cycloidal.step]
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2024-07-28 Fixed screw and wire pins, started assembly with bearings
    Onshape: https://cad.onshape.com/documents/c861ec30af8169cf9c14bd7f/w/e538486c85e6a5fe77cd1d33/m/50b4d15f6b5c681f1f2e4d89/e/395711bbc38dcc987be1be1a
    [Cycloidal.step]
2024-07-28 Working on partial assembly, added parts used
    I added some of the parts I designed that were found in the model files but hadn't been separated into their own parts.
    Onshape: https://cad.onshape.com/documents/c861ec30af8169cf9c14bd7f/w/e538486c85e6a5fe77cd1d33/m/1463a26025bf83d2a42cbf99/e/7383c3da91d908f3c2a75881
    [Carbon Fiber Rod.step, Cycloidal Assembly.step, Cycloidal.step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]
2024-07-29 Tolerance adjustments and adding bearing
    I tweaked a lot of the tolerances, and added bearings around all the little rods.
    Onshape: https://cad.onshape.com/documents/c861ec30af8169cf9c14bd7f/w/e538486c85e6a5fe77cd1d33/m/66f398e2432e977fad1e9c49/e/395711bbc38dcc987be1be1a
    [Cycloidal Assembly.step, Cycloidal.step]
2024-07-29 Working on output stage
    I realized there is a mistake with my 2nd cycloidal disc. It should be rotated 180 degrees *before* I add holes.
    Onshape link: https://cad.onshape.com/documents/c861ec30af8169cf9c14bd7f/w/e538486c85e6a5fe77cd1d33/m/784a39689ffc65992edb9c4b/e/7383c3da91d908f3c2a75881
    [Cycloidal.step]
2024-07-29 Fixed 2nd disc, working on output stage
    Onshape: https://cad.onshape.com/documents/c861ec30af8169cf9c14bd7f/w/e538486c85e6a5fe77cd1d33/m/98de684524afdfbcdc4f0564/e/7383c3da91d908f3c2a75881
    [Cycloidal.step]
2024-07-29 Sensor mount for top
    I designed a sensor mount for the top, which is mostly finished. The wires have to be splayed out then follow guides to the underside of the sensor, so I can actually screw the gearbox together.
    Onshape: https://cad.onshape.com/documents/c861ec30af8169cf9c14bd7f/w/e538486c85e6a5fe77cd1d33/m/b6f17e62d791b64e682bc9b3/e/7383c3da91d908f3c2a75881
    [Cycloidal.step]
2024-07-29 Finished sensor mount
    Unfortunately the magnet needed for encoding is sticking out the top quite a bit. The only way I could fix this is if I remove the sensor from the on axis position and moved it to the side, which would require a pcb redesign. I could also decrease the height a little bit if the whole sensor could nestle in the screws instead of being on top.
    Onshape: https://cad.onshape.com/documents/c861ec30af8169cf9c14bd7f/w/e538486c85e6a5fe77cd1d33/m/034e83fa55fcec580c0735db/e/7383c3da91d908f3c2a75881
    [Cycloidal.step]
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2024-07-29 Work in progress shrinking design
    I changed the shape of the screw standoffs, its a work in progress fixing all the broken references.
    Onshape: https://cad.onshape.com/documents/c861ec30af8169cf9c14bd7f/w/e538486c85e6a5fe77cd1d33/m/cd530b5a5eb177d17b915d6c/e/7383c3da91d908f3c2a75881
    [Cycloidal.step]
2024-07-29 Still fixing broken references
    Onshape https://cad.onshape.com/documents/c861ec30af8169cf9c14bd7f/w/e538486c85e6a5fe77cd1d33/m/b95fba314a62f127e0e52bbb/e/7383c3da91d908f3c2a75881
    [Cycloidal.step]
2024-07-30 Fixed the gearbox and assembly
    The diameter is now 3mm smaller! Not visibly noticeable though. I can still decrease the height.
    Onshape: https://cad.onshape.com/documents/c861ec30af8169cf9c14bd7f/w/e538486c85e6a5fe77cd1d33/m/f6b3977b89de95e26f490331/e/395711bbc38dcc987be1be1a
    [Cycloidal Assembly.step, Cycloidal.step]
2024-07-30 Animated cycloidal
    Note that the changes are only visible in Onshape really
    Onshape: https://cad.onshape.com/documents/c861ec30af8169cf9c14bd7f/w/e538486c85e6a5fe77cd1d33/m/0fd09e6c676fce52f4df5401/e/395711bbc38dcc987be1be1a
    [Cycloidal Assembly.step, Cycloidal.step]
2024-07-30 Quick fix reduction ratio on outside gearbox
    The output tooth count was one more than it should have been, because I changed the reduction ratio value to be the actual reduction ratio and not the inner tooth count.
    Onshape: https://cad.onshape.com/documents/c861ec30af8169cf9c14bd7f/w/e538486c85e6a5fe77cd1d33/m/a3c9333dac0244a404873054/e/395711bbc38dcc987be1be1a
    [Cycloidal Assembly.step, Cycloidal.step]
2024-07-31 Added STL files and Lychee slicer profile, tweaked dimensions after failed
    I got a terrible print, with a ton of flakes and a lot of snapped stuff. All the big parts failed too. Of the parts that didn't fail, I was able to test fit, so I tweaked some dimensions.
    [Cycloidal - 1st disk.stl, Cycloidal - 2nd disc.stl, Cycloidal - base gearbox plate.stl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]
2024-08-02 Fixing tolerances
    I've gone through several print iterations on this already.
    Things I've changed
    - Increase bearing flange holders from 0.2 to 0.5mm
    - Increased wire hole diameter
    - Added tolerance to the cycloidal disc
    - Change orientation in Lychee slicer to print upright as that's more dimensionally accurate
    - Changed Resin settings to have longer exposure to help failures. I also changed the FEP film on my printer
    [Cycloidal - 1st disk.stl, Cycloidal - 2nd disc.stl, Cycloidal - base gearbox plate.stl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]
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2024-08-06 Finished pinout
    I now have 4 motors taken care of, SPI control, another spi for sensors, and 2 extra gpio for an analog sensor and an LED. It is completely full. I need to double check everything still for pin problems
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2024-08-06 Working ESP32-s3, tight gearbox
    The gearbox base is too tight around the motor, causing binding. I can rotate by hand alright, but the motor cannot spin.
    [Motor_tests_ESP32-S3.ino]
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2024-08-07 Start redesign of encoder board for flex circuit
    [MA735 encoder board.kicad_pcb, MA735 encoder board.kicad_sch]
2024-08-07 Partial layout complete
    I currently have the board sized at 4.5mm with a really long cable. This is probably WAY to small, I can barely fit the 0402 capacitors.
    [MA735 encoder board.kicad_pcb, MA735 encoder board.kicad_sch]
2024-08-07 Mostly completed routing
    I have reached the minimum obtainable space, 5.6mm diameter. I don't think is not worth it to try shrinking it smaller
    [MA735 encoder board.kicad_pcb]
2024-08-10 Updated LICENSE
    Switched from a permissive MIT license to a dual license covering hardware (CERN-OHL) and software(GPLv3).
    [MCU.kicad_sch, MOSFET.kicad_sch, Power.kicad_sch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]
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2024-08-10 Changed everything to 0.2mm traces and 0.3mm vias for cost
    Its a tight fit but everything works out okay. Note that the trace minimum gap is half of the typical, its at 0.1mm. Most board manufactures should be able to handle this, but it may still add an additional cost
    [MA735 encoder board.kicad_pcb]
2024-08-11 Finished Magnetic encoder flex pcb
    I added a hatched ground plane. I also re-arranged the filter capacitors so the clock signal could get out without needing vias. There is much more room now with the wiring
    [MA735 encoder board.kicad_pcb, MA735 encoder board.kicad_sch]
2024-08-13 Fixed longstanding silkscreen bug
    Mosi and Miso were swapped
    [stm32g070 and DRV8311 single motor board - V1 Alpha.kicad_pcb]
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2024-08-13 Mostly finished draft wiring
    I added test points to practically every pin I won't be using regularly. Even if I never use a pin, it is better to have it exposed somehow than to try to solder to a tiny pitch pad
    [PSU.kicad_sch, esp32-s3 and DRV8311 single motor board.kicad_sch]
2024-08-14 Finished schematic and fixed DRC errors
    Now I'm moving on to layout.
    [PSU.kicad_sch, esp32-s3 and DRV8311 single motor board.kicad_pcb, esp32-s3 and DRV8311 single motor board.kicad_sch]
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2024-08-14 Wiring some signal wires and moving power around to accomodate
    There are location conflicts left and right! I will eventually get this mess sorted out, but I am wondering about 6 layer boards and blind vias. 4 layers will keep the costs down though!
    [DRV8311.kicad_sch, esp32-s3 and DRV8311 single motor board.kicad_pcb, esp32-s3 and DRV8311 single motor board.kicad_sch]
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2024-08-17 Fixed DRC errors
    I still have to fix all the silkscreen issues
    [esp32-s3 and DRV8311 single motor board.kicad_pcb]
2024-08-17 Fixed Silkscreen
    [DRV8311.kicad_sch, esp32-s3 and DRV8311 single motor board.kicad_pcb]
2024-08-17 Switched Shift register lines to USB
    The shift register will be virtually unaffected by any USB activity, and the usb lines should not be affected at low speeds for having a shift register on the bus. In my final design I will be using 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
    [esp32-s3 and DRV8311 single motor board.kicad_pcb, esp32-s3 and DRV8311 single motor board.kicad_sch]
2024-08-17 Started migrating driver to the back of the motor
    If successful, this will save a ton of space. This will be a mess for awhile.
    [Bottom motor Drawing.dxf, DRV8311 on motor driver.kicad_pcb, DRV8311 on motor driver.kicad_sch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]
2024-08-18 Fixed kicad schematic errors, arranged pads
    [DRV8311 on motor driver.kicad_pcb, DRV8311 on motor driver.kicad_sch]
2024-08-18 Finished component layout
    The current board diameter is 12mm, though I may be able to shrink it down to 10mm. Its already REALLY small, with those 0402 components. It would be nice if the board didn't exceed the outer diameter of the motor.
    [DRV8311 on motor driver.kicad_pcb, DRV8311 on motor driver.kicad_sch]
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2024-08-18 Complex wire re-arranging
    The most difficult to route wires are those last ones, the input and output wires. I have spent a long time figureing out an arrangement that would allow me to connect that. I wish I could add vias i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
    [DRV8311 on motor driver.kicad_pcb]
2024-08-18 Finished routing, distribute pwr planes, silkscreen and DRC check
    The power planes were not making good connection previously, so I have fixed that.
    Silkscreen is done, the last traces have been routed, and there isn't much I can do
    As far as I'm concerned, this board is done!
    [DRV8311 on motor driver.kicad_pcb, DRV8311 on motor driver.kicad_sch]
2024-08-18 Removed drv8311 section on the main board
    Don't need it now that I have it off-board.
    [esp32-s3 single motor & battery controller.kicad_pcb]
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2024-08-21 Starting work on replacing battery charger with 2s version
    The charger module will be way too big, but I really think I need this. Hopefully I can find a more integrated charger
    [PSU.kicad_sch]
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2024-08-23 Finished PSU schematic, Fixed ERC errors
    [PSU.kicad_sch, esp32-s3 single motor & battery controller.kicad_sch]
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2024-08-24 Almost complete charger section, working on balancer
    I have a problem with the current sense lines on the balance charger. One loops around with filter capacitors, while the other zigs and zags back and forth on multiple layers! They have to cross each other, and this may lead to a lot of noise.
    [PSU.kicad_sch, esp32-s3 single motor & battery controller.kicad_pcb]
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2024-08-24 Running DRC and fixing footprints
    I had to fix the footprints of the driver chip and the shift register, because there were some undefined pads and the vias were too small.
    [esp32-s3 single motor & battery controller.kicad_pcb, esp32-s3 single motor & battery controller.kicad_sch]
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2024-08-24 Removed battery voltage divider, fixed BATTPres indicator
    [PSU.kicad_sch, esp32-s3 single motor & battery controller.kicad_pcb, esp32-s3 single motor & battery controller.kicad_sch]
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2024-08-25 Making a few changes to layout based on spotted problems
    [PSU.kicad_sch, esp32-s3 single motor & battery controller.kicad_pcb]
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2024-08-25 Routed pullup resistors, replace Bat Pres trace with pad
    I now have several lines routed on the ground plane, but I tried to minimize the used space
    [PSU.kicad_sch, esp32-s3 single motor & battery controller.kicad_pcb]
2024-08-25 Silkscreen and smd clearance cleanup
    Everything was complete, but I identified a new issue on the board to fix soon. I will have to switch the battery balance chip to the other side of the board to be closer to the current sense resistor and minimize losses.
    [esp32-s3 single motor & battery controller.kicad_pcb]
2024-08-25 Fixed small issue on Driver board resistor values swapped
    I switched it from 100k over 300k, to 300k over 100k. If the input is 8.4 volts, the output should be 2.1 volts. Small mistake.
    [DRV8311 on motor driver.kicad_pcb, DRV8311 on motor driver.kicad_sch]
2024-08-25 Swapped sides for battery balance IC
    This actually simplifies routing a lot, since the current sense lines are on the same side.
    [PSU.kicad_sch, esp32-s3 single motor & battery controller.kicad_pcb]
2024-08-25 Fixing routing issues after change
    [PSU.kicad_sch, esp32-s3 single motor & battery controller.kicad_pcb]
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2024-08-26 Started redesign of cycloidal gearbox
    Onshape: https://cad.onshape.com/documents/c861ec30af8169cf9c14bd7f/w/e538486c85e6a5fe77cd1d33/m/fec7b2625313921ff504b536/e/7383c3da91d908f3c2a75881
    [Cycloidal.step]
2024-08-26 Added sensor flex cable routing and reduced vertical space
    The top is now flush, since I have chosen a different magnet.
    I also added some support towers back in, including a new one for the sensor flex cable.
    Onshape: https://cad.onshape.com/documents/c861ec30af8169cf9c14bd7f/w/e538486c85e6a5fe77cd1d33/m/7b5e3d6ef87d963f5ec9f7a0/e/7383c3da91d908f3c2a75881
    [Cycloidal.step]
2024-08-26 Correct pin diameters and simplified pins for cycloidal
    Onshape: https://cad.onshape.com/documents/c861ec30af8169cf9c14bd7f/w/e538486c85e6a5fe77cd1d33/m/e3e226d39e0a8cf9c0a1df9a/e/7383c3da91d908f3c2a75881
    [Cycloidal.step]
2024-08-26 Fixed top screw holes, added encoder pcb holder
    Onshape: https://cad.onshape.com/documents/c861ec30af8169cf9c14bd7f/w/e538486c85e6a5fe77cd1d33/m/a44ac8d92326f56f018b54d6/e/7383c3da91d908f3c2a75881
    [Cycloidal.step]
2024-08-27 Fixing magnet top and flex cable path
    Onshape: https://cad.onshape.com/documents/c861ec30af8169cf9c14bd7f/w/e538486c85e6a5fe77cd1d33/m/3281a3f827947617db59824e/e/7383c3da91d908f3c2a75881
    [Cycloidal.step]
2024-08-27 Fixed 2nd cycloidal disc, and assembly
    Onshape: https://cad.onshape.com/documents/c861ec30af8169cf9c14bd7f/w/e538486c85e6a5fe77cd1d33/m/05a395521fa38bfb81dc69eb/e/7383c3da91d908f3c2a75881
    [Cycloidal.step]
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2024-08-31 Fixed gear ratios for 3 planets
    I forgot the sun and the ring for BOTH stages has to be divisible by 3. I fixed that now. Total output ratio is now 74.66:1.
    Onshape: https://cad.onshape.com/documents/c861ec30af8169cf9c14bd7f/w/e538486c85e6a5fe77cd1d33/m/03cf66b45418e8ea5545b44a/e/c076bfebf996b33c466ae250
    [Split Ring Compound Plantery.step]
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

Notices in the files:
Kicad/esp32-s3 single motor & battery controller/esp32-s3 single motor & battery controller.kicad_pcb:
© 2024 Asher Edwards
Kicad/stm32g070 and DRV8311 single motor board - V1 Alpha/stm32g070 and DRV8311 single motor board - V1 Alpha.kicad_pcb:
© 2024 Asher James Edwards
